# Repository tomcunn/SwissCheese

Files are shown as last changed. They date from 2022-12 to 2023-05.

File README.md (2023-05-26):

# SwissCheese
Virtual Swiss Cheese Game

Creating a environment for the game of jeu gruyere using pygame.

https://makezine.com/projects/the-game-of-jeu-gruyere/

#Inputs
The input into the system will always be the length of the cord regardless of what control method is used. 

# Goals
The goal is to solve this a couple of ways:

* Manually by controlling the cords
* Using motors to run the inverse kinematics to allow control of x,y via a joystick
* AI algorithm that controls the lengths of the cords
* AI algorithm that controls the x,y position, and then computes the lengths of cords

# Stepper Motors
For the motion axes, going to try to use stepper motors running some GT2 belt in order to maintain position. The stepper motors are used because the RAMPS 1.6

board was available and does not requrie me to make a PCB for this project as the RAMPS already supports all of the I/O that are required, including some FETS for the solenoid on the crane project. 

The engineering challenge here is creating a dual axes motion control. The inverse and forward kinematics are solved in the python game script. The motion control consists of generating timing pulses to control the stepper motors which is pretty straightforward. The issue becomes how to control both of the motors when going between two different points.

```
 X  (start)
  \
   \
    \ 
     X (end)
```   
The delta Y here is larger than the delta X, so the Y axes must move faster than X axis such that both of them arrive at the same time. The issue is that the machine is not linear, so the angle of the cables come into place. 

# Kinematics
The arduino only uses the inverse kinematics. 

```
#Set the kinematics type to use
#FORWARD - Control the lengths of the cords , then compute x,y
#INVERSE - Control the x,y , then compute lengths
KINEMATICS_TYPE = 'INVERSE'
```

Here are the kinematics for the two cable. 

```
.
(0,0)
  A    ab    B
   \       /
    \     /
 ad  \   / bd
      \ /
       D
#Given x,y (0,0) is top left and the length between the two joints, compute the ad and bd

    ad = math.sqrt(dx*dx+yx*yx)
    bd = math.sqrt((Bx-x)*(Bx-x)+y*y)
   
```

# Path Planning

How do you go from (2,10) to (5,5), with (0,0) being the upper left. The delta is 3 in the X, and is 5 in the Y. Maybe we just simply have a master axis, and then have a dependent axis. Meaning that we command the X to 10 inches/min, and then we know that X needs to travel 5/3 faster, so we command the Y to 16.66 inches/min. The difficult becomes what about the acceleration phase and computing time and position to sync the two axes. The next question is what is good enough. For manual control 

# Hardware Hookup

```
//These pins have been verified to work
#define X_STEP    A0
#define X_DIR     A1
#define X_ENABLE  38

#define Z_STEP    46
#define Z_DIR     48
#define Z_ENABLE  A8
```

The stepper motor connection to the RAMPS 1.6 Board. 



So far this appears to be the pinout of the RAMP 1.6 Board.



# Dual Joystick Control

Creating a dual joystick to demo. There will be two modes:

 * Each joystick y controls the length (no kinematics required, the human does the kinematics)
 * One joystick controls the x,y 

```
//Joystick Wiring
Wire Color    Physical  Jumper Board   MEGA
Green/White   5V         Power          5V
Blue          Gnd        Gnd            GND
Orange/White  Right Y    AN0            A3
Orange        Left Y     AN1            A4
Blue/White    Right X    Switch A       A5
Brown/White   Toggle     Switch B       D44
```

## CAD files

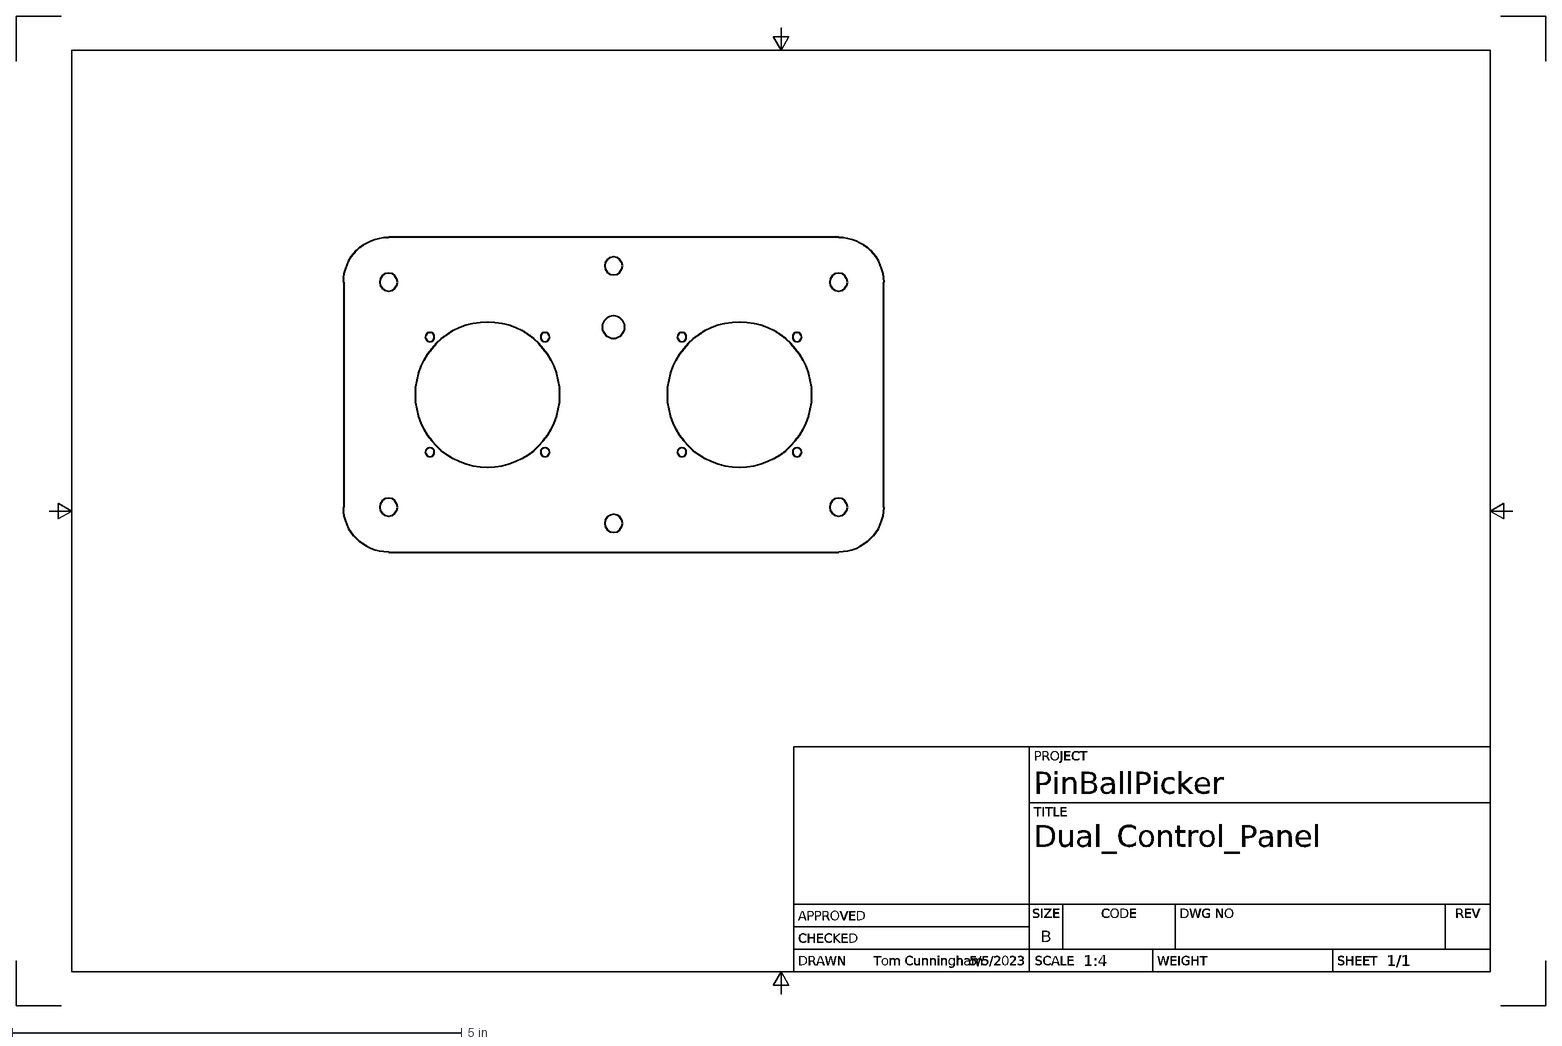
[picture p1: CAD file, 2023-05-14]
Mechanical/DualJoystickControlPanel/Dual_Control_Panel Drawing v2.dxf
1/1
1:4
5/5/2023
Tom Cunningham
B
PinBallPicker
Dual_Control_Panel
PROJECT
TITLE
DRAWN
CHECKED
APPROVED
SCALE
WEIGHT
SHEET
DWG NO
REV
CODE
SIZE

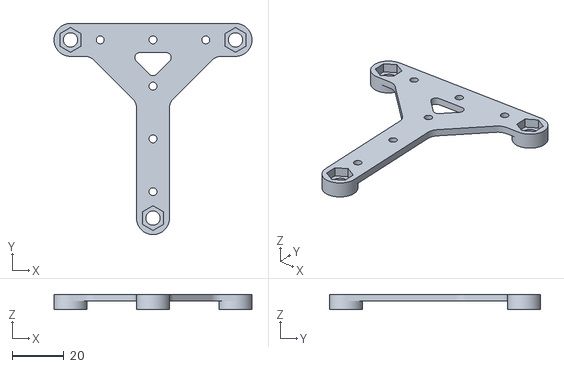
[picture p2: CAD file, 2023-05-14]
Mechanical/StepperMotorMountBracket/StepperMotorMountBracket.stl
76.2 x 81.3 x 5.71

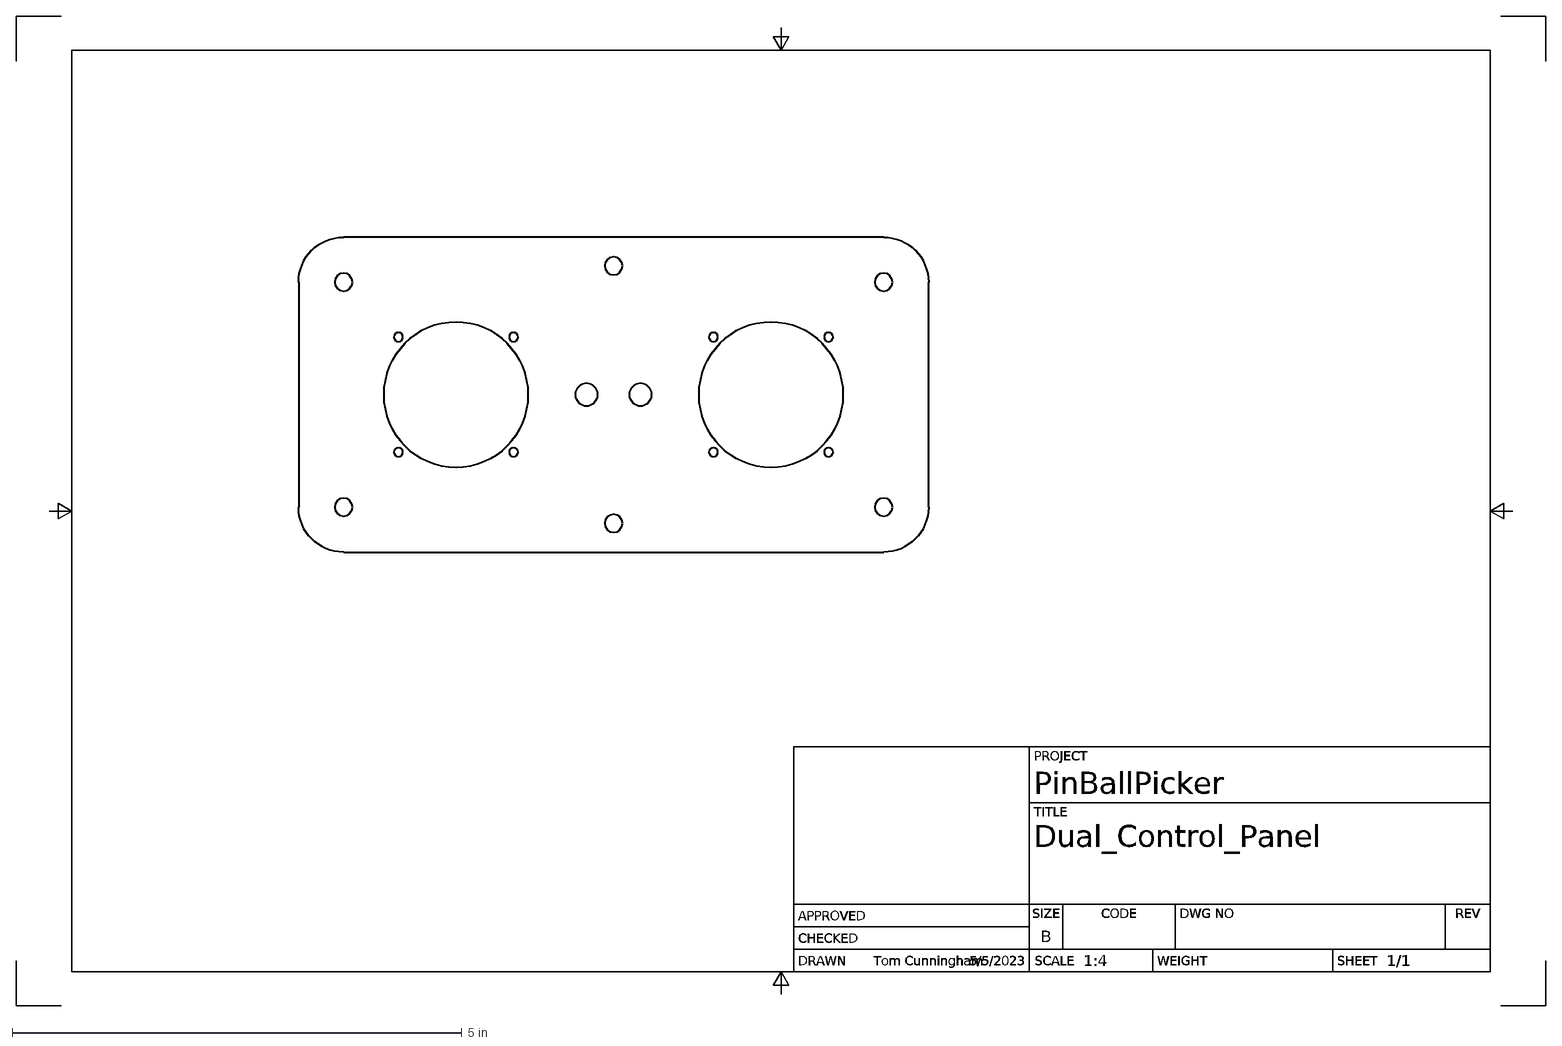
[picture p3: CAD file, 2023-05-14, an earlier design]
Mechanical/DualJoystickControlPanel/Dual_Control_Panel Drawing v1.dxf
1/1
1:4
5/5/2023
Tom Cunningham
B
PinBallPicker
Dual_Control_Panel
PROJECT
TITLE
DRAWN
CHECKED
APPROVED
SCALE
WEIGHT
SHEET
DWG NO
REV
CODE
SIZE

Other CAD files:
Mechanical/StepperMotorMountBracket/MotorPlateLongMount v6.f3d
Mechanical/StepperMotorMountBracket/StepperMotorMountBracket.f3d

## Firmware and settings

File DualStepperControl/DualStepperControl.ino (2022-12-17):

//**************************************
//*   Stepper Motor Control
//*
//*   Cloned from the AI project
//*   12/11/2022
//*   Cunningham
//***************************************

#include <avr/io.h>
#include <avr/interrupt.h>

#define PRINT_XY
#define PRINT_JOINTS
#define PRINT_STEPS

//Hardware Assignments
#define  MAX_VELOCITY  90000
#define  MAX_ACCELERATION  2000
#define  ERROR_TOLERANCE 100

#define StepA    A0
#define DirA     A1
#define EnableA  38

#define StepB    46
#define DirB     48
#define EnableB  A8

//Function prototypes
void  SetupTimer1              (void);
void  SetupTimer0              (void);
void  MotionAccelerationControl(struct MovementParms *MotorCurrent, struct MovementParms *MotorDesired);
void  MotionVelocityControl    (struct MovementParms *MotorCurrent, struct MovementParms *MotorDesired);
void  ForwardKinematics        (struct Joint_Distances *JointLength, struct Coordinates *CurrentCoordinates);
void  InverseKinematics        (unsigned int x, unsigned int y, struct Joint_Distances *JointLength);
void  WriteStepSize            (struct MovementParms *Motor);
void  ReadJoystick             (struct Coordinates *lDesiredCoordinates);

static int counter=0;

//394mm is the initial joint length.

#define Bx_distance 470 //18.5 inches
#define Steps_per_mm 27.03f  * 2  //Added the x2 because we changed to a higher frequency get 50% duty cycle. Now we interrupt on the rising and falling edge of the pulse. 

#define MAX_X 450
#define MAX_Y 550

//Create a structure for movement data
struct MovementParms
{
  signed long  Position;          // steps  - Everytime the interrupt is triggered, this occurs
  signed int   Velocity;          // 
  signed int   Acceleration;      //
  unsigned int TimerMatchValue;   //
  bool         Direction;         //
  bool         Hold;              //
};

struct Joint_Distances
{
   float AD;               // mm
   float BD;               // mm
   float AB;               // mm
};




struct Coordinates
{
  float x;
  float y;
};

//Create instance of three structures 
volatile struct MovementParms MotorA_Desired;
volatile struct MovementParms MotorA_Current;
volatile struct MovementParms MotorB_Desired;
volatile struct MovementParms MotorB_Current;


struct MovementParms LinearMotion;
struct Joint_Distances Joints;
struct Coordinates CurrentCoordinates;
struct Coordinates DesiredCoordinates;


//Static Variables that are accessed in interrupts
volatile unsigned int abs_Current_Velocity = 0;
static volatile unsigned int Counter = 0;
static volatile unsigned int StepSpeedA = 0;
static volatile unsigned int StepSpeedB = 0;
static volatile unsigned int tempA = 0;
static volatile unsigned int tempB = 0;
static volatile signed long timestep = 0;
static volatile bool RunTask_10ms = 0;
static volatile bool flopa = 0;
static volatile bool flopb = 0;


//Kinematics (distance in mm)
//  A(0,0)        B(100,0)
//   A          B
//     \       /
//      \     /
//       \   /
//         D
//Given x,y, find the distances AD, BD
void InverseKinematics(unsigned int x, unsigned int y, struct Joint_Distances *JointLength)
{
  float x2 = (float)x * x;
  float y2 = (float)y * y;
  
  JointLength->AD = (float)sqrt(x2+y2);
  JointLength->BD = sqrt(((float)Bx_distance-x)*(Bx_distance-x)+y2);
}


//Given the joint lengths, determine the position x,y
void ForwardKinematics(struct Joint_Distances *JointLength, struct Coordinates *Coord)
{
  float AD2 = JointLength->AD * JointLength->AD;
  float BD2 = JointLength->BD * JointLength->BD;

  float x = (AD2 - BD2 + ((float)Bx_distance * Bx_distance)) / (2 * Bx_distance);
  float y2 = AD2 - (x * x);

  if(y2 < 0) return -1;
    Coord->x = x;
    Coord->y = sqrt(y2);
  return 0;
}


//**************************************
// Timer1 - 16 bit timer Interrupt  
// Motor A
// Setup for ATMEGA2560
//**************************************
ISR(TIMER4_COMPA_vect)  
{   
     //Check the direction pin and determine the position
    if(MotorA_Current.Hold == false)
    {
      if(MotorA_Current.Direction == 1)
      {
          digitalWrite(DirA,1);
          MotorA_Current.Position++;
      }
      else
      {
        digitalWrite(DirA,0);
        MotorA_Current.Position--;
      }
      
      if(flopa)
      {
          digitalWrite(StepA,1);
          flopa = 0;
      }
      else
      {
          digitalWrite(StepA,0);
          flopa=1;
      }
    }
   //tempA =StepSpeedA;
   OCR4A= StepSpeedA;
  
}

//**************************************
// Timer3 - 16 bit timer Interrupt 
// Motor B 
// Setup for ATMEGA2560
//**************************************
ISR(TIMER3_COMPA_vect)  
{   
    if(MotorB_Current.Hold == false)
    {
      //Check the direction pin and determine the position
      if(MotorB_Current.Direction == 1)
      {
         digitalWrite(DirB,0);
         MotorB_Current.Position++;
      }
      else
      {
         digitalWrite(DirB,1);
         MotorB_Current.Position--;
      }


      if(flopb)
      {
         digitalWrite(StepB,1);
         flopb = 0;
      }
      else
      {
         digitalWrite(StepB,0);
         flopb=1;
      }
    }
   //tempB = StepSpeedB;
   OCR3A =  StepSpeedB;
}

//**************************************
// Timer0 - 8 bit timer Interrupt  
// Setup for ATMEGA2560
//**************************************
ISR(TIMER0_COMPA_vect)
{
  //Check to see if the flag was not cleared, this will track 
  //overruns in the 10ms task
  if(RunTask_10ms)
  {
    digitalWrite(LED_BUILTIN,1);
  }
  RunTask_10ms = 1;
}


//*******************************************
// WriteStepSize
//
// Pass in a velocity and update the step size
// global variable which is read by the interrupt
// to generate the stepper pulses. Speed is in 
// the units mm/min. 
//*******************************************
void WriteStepSize(struct MovementParms *Motor)
{
  unsigned int StepSpeed = 0;
  //Set the direction pin based on the sign of the speed
  if(Motor->Velocity > 0)
  {
     Motor->Direction = 1;
  }
  else
  {
     Motor->Direction = 0;
  } 
  // Conversion Factor in One Note
  // 1:1 Prescale = 16,000,000Hz
  // 200*16microsteps = 3200 steps/rev
  // 27.03 steps/mm

  //Check to prevent overflows, StepSpeed is 16 bit
  // 700 mm/sec is VERY slow, 0.25 rev/sec.
  if(((Motor->Velocity) > 700) || ((Motor->Velocity) < -700))
  {
     //This is derived from the table above using a Power trendline
      Motor->TimerMatchValue = (unsigned int)(16000000L/(abs(Motor->Velocity)));
  }
  //This is like setting it to zero speed
  else
  {
   Motor->TimerMatchValue = 65000;
     
  }
}
//*******************************************
//  Configure Timer 1 - 16 bit timer
//  Atmega2560
//  Timer/Counter 1, 3, 4, and 5
//*******************************************
void SetupTimer4()
{
  //Clear the register
  TCCR4A = 0;
  TCCR4B = 0;

  //Set the prescaler
  TCCR4B|=(1<<CS10);// Clock/1

  //Start counting at zero and then interrupt on match
  TCCR4B|=(1<<WGM12); // Set in CTC mode

  //The value of the match.
  OCR4A=0; // Set Output compare to 250;

  TIFR4 = 0xFF;


}

//*********************************************
//  Configure Timer 3
//*********************************************
void SetupTimer3()
{
  //Clear the register
  TCCR3A = 0;
  TCCR3B = 0;

  //Set the prescaler
  TCCR3B|=(1<<CS10);// Clock/1

  //Start counting at zero and then interrupt on match
  TCCR3B|=(1<<WGM12); // Set in CTC mode

  //The value of the match.
  OCR3A=0; // Set Output compare to 250;
 
  TIFR3 = 0xFF;

}

//*********************************************
//  Configure Timer 0
//  Page 115
//*********************************************
void SetupTimer0()
{

  TCCR0A = 0; // set entire TCCR0A register to 0
  TCCR0B = 0; // same for TCCR0B
  TCNT0  = 0; //initialize counter value to 0
  // set compare match register for 2khz increments
  OCR0A = 155;// = (16*10^6) / (100*1024) - 1 = 155(must be <256)
  // turn on CTC mode
  TCCR0A |= (1 << WGM01);
  // 1024 prescaler - page 142 of datasheet
  TCCR0B |= (1 << CS00); 
  TCCR0B |= (1 << CS02);  
  // enable timer compare interrupt
  TIMSK0 |= (1 << OCIE0A);
}

//*****************************************
//  Main Setup Function
//
//
//*****************************************
void setup() 
{
  //Disable interrupts
  cli();
  
  //Set the pin modes
  pinMode(StepA,OUTPUT);
  pinMode(DirA,OUTPUT);

  pinMode(StepB,OUTPUT);
  pinMode(DirB,OUTPUT);

  pinMode(EnableA,OUTPUT);
  pinMode(EnableB,OUTPUT);

  pinMode(A3,INPUT);
  pinMode(A4,INPUT);

  digitalWrite(EnableA, LOW);
  digitalWrite(EnableB, LOW);

  MotorA_Current.Hold = true;
  MotorB_Current.Hold = true;

  //Setup Timers
  SetupTimer3();
  SetupTimer4();
  SetupTimer0();
  delay(1000);
  
  Serial.begin(115200);

  Serial.println("This is the setup TCCR1A");
  Serial.println(TCCR1A);

  Serial.println("This is the setup TCCR3A");
  Serial.println(TCCR3A);

  Serial.println("This is the setup TCCR1B");
  Serial.println(TCCR1B);

  Serial.println("This is the setup TCCR3B");
  Serial.println(TCCR3B);

  digitalWrite(DirB,1);
  digitalWrite(DirA,1);

  //Need to start in a known position, this needs to be in steps, not mm
  MotorA_Current.Position = (signed long)394 * Steps_per_mm;
  MotorB_Current.Position = (signed long)394 * Steps_per_mm ;

  DesiredCoordinates.x = 235;
  DesiredCoordinates.y = 316;

  delay(2000);

  //enable interrupts
  sei();
  
}


//********************************************
//  Main Loop
//********************************************
void loop() 
{
  static bool FirstLoop = true;

  if(RunTask_10ms)
  {
    //Determine the x,y desired
    ReadJoystick(&DesiredCoordinates);

    #ifdef PRINT_XY
    Serial.print(DesiredCoordinates.x);
    Serial.print(",");
    Serial.print(DesiredCoordinates.y);
#endif //PRINT_XY

    //Compute the joint lengths, pass in mm
    InverseKinematics(DesiredCoordinates.x,DesiredCoordinates.y ,&Joints);

#ifdef PRINT_JOINTS
    Serial.print(",");
    Serial.print(Joints.AD);
    Serial.print(",");
    Serial.print(Joints.BD);
#endif //PRINT_JOINTS
    
    //Assign the joint length to the corresponding motor system
    MotorA_Desired.Position = (signed long)(Joints.BD * Steps_per_mm);
    MotorB_Desired.Position = (signed long)(Joints.AD * Steps_per_mm);
    
    //Compute the motion profile based on the position error
    MotionPositionControl(&MotorA_Current, &MotorA_Desired);
    MotionPositionControl(&MotorB_Current, &MotorB_Desired);

#ifdef PRINT_STEPS
    Serial.print(",");
    Serial.print(MotorA_Desired.Position);
    Serial.print(",");
    Serial.print(MotorA_Current.Position);
#endif //PRINT_JOINTS

    //Call function to covert the velocity from mm/min to timer value
    WriteStepSize(&MotorA_Current);
    WriteStepSize(&MotorB_Current);

    //The StepSpeed is used by the interrupt
    StepSpeedA = MotorA_Current.TimerMatchValue;
    StepSpeedB = MotorB_Current.TimerMatchValue;

    //Compute the current position that the machine is in.
    ForwardKinematics(&Joints,&CurrentCoordinates);

#ifdef PRINT_XY
    Serial.print(",");
    Serial.print(CurrentCoordinates.x);
    Serial.print(",");
    Serial.println(CurrentCoordinates.y);
#endif //PRINT_XY

    if(FirstLoop)
    {
      //Enable to interrupt on timer 1
      TIMSK3 |= (1<<OCIE3A); 
      ////Enable to interrupt on timer 1
      TIMSK4 |= (1<<OCIE4A);
      // 
      FirstLoop = false;
    }

    //Clear the flag that gets set by the interrupt
    //This was added at end to detect overruns of the 10ms task
    RunTask_10ms = 0;
  }
}


//*********************************************
// MotionPositionControl
//*********************************************
void MotionPositionControl(struct MovementParms *MotorCurrent, struct MovementParms *MotorDesired)
{
  signed long Position_Error;

  //Compute the error 
  //Positive value means the cable is too short, this is in steps
  Position_Error = (MotorDesired->Position) - (MotorCurrent->Position);
 
  //The cable is too short, make it longer
  if(Position_Error > ERROR_TOLERANCE)
  {
     MotorCurrent->Velocity = 1000;
     MotorCurrent->Hold = false;
  }
  //The cable is too long, make it shorter
  else if(Position_Error < -ERROR_TOLERANCE)
  {
     MotorCurrent->Velocity = -1000;
     MotorCurrent->Hold = false;
  }
  //Just the right length
  else
  {
     MotorCurrent->Velocity = 10;
     MotorCurrent->Hold = true;
  }
}

//*********************************************
// MotionVelocityControl
//*********************************************
void MotionVelocityControl(struct MovementParms *MotorCurrent, struct MovementParms *MotorDesired)
{  
  //Moving in the positive direction
  if(MotorCurrent->Velocity >= 0)
  
     //Determine if we are speeding up
     if(MotorCurrent->Velocity < MotorDesired->Velocity)
     {
        //Check to see if we can add the acceleration without overshooting
        if(MotorCurrent->Velocity < (MotorDesired->Velocity - MotorDesired->Acceleration))
        {
           MotorCurrent->Velocity += MotorDesired->Acceleration;
        }
        else
        {
           MotorCurrent->Velocity = MotorDesired->Velocity;
        }
     }
     //We are slowing down 
     else
     {
        //Check for overshoot
        if(MotorCurrent->Velocity > (MotorDesired->Velocity + MotorDesired->Acceleration))
        {
           MotorCurrent->Velocity -= MotorDesired->Acceleration;
        }
        else
        {
           MotorCurrent->Velocity = MotorDesired->Velocity;
        }
     }
  //Moving in the negative direction, all the signs flip   
  else
  {
     //Determine if we are speeding up
     if(MotorCurrent->Velocity > MotorDesired->Velocity)
     {
        //Calculate the timer for the next pulse
        if(MotorCurrent->Velocity > (MotorDesired->Velocity + MotorDesired->Acceleration))
        {
           MotorCurrent->Velocity -= MotorDesired->Acceleration;
        }
        else
        {
           MotorCurrent->Velocity = MotorDesired->Velocity;
        }
     }
     //We are slowing down 
     else
     {
        //Calculate the timer for the next pulse
        if(MotorCurrent->Velocity < (MotorDesired->Velocity - MotorDesired->Acceleration))
        {
           MotorCurrent->Velocity += MotorDesired->Acceleration;
        }
        else
        {
           MotorCurrent->Velocity = MotorDesired->Velocity;
        }
     }
  }
}

//***********************************
//  MotionAccelerationControl
//
//
//***********************************
void MotionAccelerationControl(struct MovementParms *MotorCurrent, struct MovementParms *MotorDesired)
{
   //Acceleration is a signed value
   //If positive check to make sure it is not bigger than max V
   //else check the - max speed
   
   if(MotorDesired->Acceleration >= 0)
   {
      if(MotorCurrent->Velocity < (MAX_VELOCITY + MotorDesired->Acceleration))
      {
         MotorCurrent->Velocity += MotorDesired->Acceleration; 
      }
      else
      {
        MotorCurrent->Velocity = MAX_VELOCITY;
      }
   }
   else
   {
      if(MotorCurrent->Velocity > (-MAX_VELOCITY + MotorDesired->Acceleration))
      {
         MotorCurrent->Velocity += MotorDesired->Acceleration;
      }
      else
      {
         MotorCurrent->Velocity = -MAX_VELOCITY;
      }
   }
}


//*****************
//  Read Joystick
//
//*****************
void ReadJoystick(struct Coordinates *lDesiredCoordinates)
{
  int vert;
  int horz;
  
  vert = analogRead(A3);
  horz = analogRead(A4);
  
  if(vert > 700)
  {
    if(lDesiredCoordinates->x < MAX_X)
    {
       lDesiredCoordinates->x = lDesiredCoordinates->x +1;
    }
  }
  else if(vert<  300)
  {
    if(lDesiredCoordinates->x > 2)
    {
       lDesiredCoordinates->x = lDesiredCoordinates->x -1;
    }
  }

  if(horz > 700)
  {
    if(lDesiredCoordinates->y < MAX_Y)
    {
      lDesiredCoordinates->y = lDesiredCoordinates->y +1;
    }
  }
  else if(horz<  300)
  {
    if(lDesiredCoordinates->y > 2)
    {
      lDesiredCoordinates->y = lDesiredCoordinates->y -1;
    }
  }


}

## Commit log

2022-07-31 Added kinematics to the model
2022-12-11 Initial Commit of stepper motor code
    Creating a generic file to control steppers motors.
2022-12-15 Added kinematics and position control
2022-12-15 updated comment, need to convert from steps to mm, trying to go 257mm, and was getting 130mm. The reason being the stating point of 100 is 100steps which about 4mm. Also need to add in a factor of 2 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
2022-12-17 Added Dualstepper2 which was reworked for velocity control.
    [StepperControl.xlsx]
2023-05-14 Adding the mechanical folder.
    [Dual_Control_Panel Drawing v1.dxf, Dual_Control_Panel Drawing v2.dxf, MotorPlateLongMount v6.f3d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]
2023-05-26 Added new project for DemoBoardDualJoystick.ino
    [StepperControl.xlsx]
2023-05-26 Untested updates for the new dual joystick demo board.
2023-06-06 Updating to the new demo board.
2023-06-06 Adding in joint mode code.
    [StepperControl.xlsx]
